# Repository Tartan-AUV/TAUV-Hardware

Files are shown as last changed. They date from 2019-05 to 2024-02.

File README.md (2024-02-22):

# TAUV-Hardware

Repository for TAUV Altium documents

# Boards:
## TAUV-PWR_STK
Next generation power management stack consisting of 2 boards. Manufacturing graciously sponsored by PCBway.com

## TAUV-Disconnect
Disconnect board for easy flange access

## TAUV-Interfacer
Utilizes a pair of STM32F7 processors to run hydrophone DOA estimates, and control/interface with LEDs, Servos, Jetson, and PowerBoard.

## TAUV-Acoustics Power Board
For powering the acoustics setup. Has low-noise 5V and 24V outputs.

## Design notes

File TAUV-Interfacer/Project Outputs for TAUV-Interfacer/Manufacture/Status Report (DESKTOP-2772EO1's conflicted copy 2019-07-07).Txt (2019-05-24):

Output: NC Drill Files
Type  : NC Drill
From  : PCB Document [TAUV-Interfacer.PcbDoc]
   Generated File[TAUV-Interfacer-RoundHoles.TXT]
   Generated File[TAUV-Interfacer-SlotHoles.TXT]
   Generated File[TAUV-Interfacer.DRL]
   Generated File[TAUV-Interfacer.LDP]
   Generated File[TAUV-Interfacer.DRR]

Files Generated   : 5
Documents Printed : 0

Finished Output Generation At 1:58:53 AM On 5/24/2019

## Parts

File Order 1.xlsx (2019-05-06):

Line # | Name | Description | Designator | Quantity | Manufacturer 1 | Manufacturer Part Number 1 | Manufacturer Lifecycle 1 | Supplier 1 | Supplier Part Number 1 | Supplier Unit Price 1 | Supplier Subtotal 1
 | #4-40 | Mounting Hole for ANSI #4-40 w/ Flat Washer, Loose Fit | MH1, MH2, MH3, MH4 | 8 |  |  |  |  |  |  |  | Power Board | Qtty: 2
 | 1K2 1% 0603(1608) | 1K2 0.1W 1% 0603 (1608 Metric) SMD | R37, R38 | 4 | Yageo (https://octopart-clicks.com/click/altium?sku=311-1.20KHRCT-ND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) | RC0603FR-071K2L (https://octopart-clicks.com/click/altium?sku=311-1.20KHRCT-ND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) | Volume Production | Digi-Key | 311-1.20KHRCT-ND (https://octopart-clicks.com/click/altium?sku=311-1.20KHRCT-ND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) | 0.024 | 0.24
 | 1K65 1% 0603(1608) | 1K65 0.1W 1% 0603 (1608 Metric) SMD | R7 | 2 | Yageo (https://octopart-clicks.com/click/altium?sku=311-1.65KHRCT-ND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) | RC0603FR-071K65L (https://octopart-clicks.com/click/altium?sku=311-1.65KHRCT-ND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) | Volume Production | Digi-Key | 311-1.65KHRCT-ND (https://octopart-clicks.com/click/altium?sku=311-1.65KHRCT-ND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) | 0.1 | 0.2
 | 1K 1% 0603(1608) | 1K 0.1W 1% 0603 (1608 Metric) SMD | R17 | 2 | Yageo (https://octopart-clicks.com/click/altium?sku=311-1.00KHRCT-ND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) | RC0603FR-071KL (https://octopart-clicks.com/click/altium?sku=311-1.00KHRCT-ND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) | Volume Production | Digi-Key | 311-1.00KHRCT-ND (https://octopart-clicks.com/click/altium?sku=311-1.00KHRCT-ND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) | 0.1 | 0.2
 | 2-pin megafit RA |  | J1, J2, J3, J4, J5, J6, J7, J8 | 16 | Molex (https://octopart-clicks.com/click/altium?sku=WM10391-ND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) | 172064-0002 (https://octopart-clicks.com/click/altium?sku=WM10391-ND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) | Manual Solution | Digi-Key | WM10391-ND (https://octopart-clicks.com/click/altium?sku=WM10391-ND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) | 2.53 | 40.53
 | 4K7 1% 0603(1608) | 4K7 0.1W 1% 0603 (1608 Metric) SMD | R19, R20 | 4 | Yageo (https://octopart-clicks.com/click/altium?sku=311-4.70KHRCT-ND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) | RC0603FR-074K7L (https://octopart-clicks.com/click/altium?sku=311-4.70KHRCT-ND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) | Volume Production | Digi-Key | 311-4.70KHRCT-ND (https://octopart-clicks.com/click/altium?sku=311-4.70KHRCT-ND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) | 0.024 | 0.24
 | 4-Pin Molex Nano-Fit | NanoFit RA Hdr TH SR 4Ckt | P3 | 2 | Molex (https://octopart-clicks.com/click/altium?sku=WM16895-ND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) | 105313-1104 (https://octopart-clicks.com/click/altium?sku=WM16895-ND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) | Manual Solution | Digi-Key | WM16895-ND (https://octopart-clicks.com/click/altium?sku=WM16895-ND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) | 1.2 | 2.4
 | 6.8uH |  | L2 | 2 | Bourns (https://octopart-clicks.com/click/altium?sku=SRP5030TA-6R8MCT-ND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) | SRP5030TA-6R8M (https://octopart-clicks.com/click/altium?sku=SRP5030TA-6R8MCT-ND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) | Volume Production | Digi-Key | SRP5030TA-6R8MCT-ND (https://octopart-clicks.com/click/altium?sku=SRP5030TA-6R8MCT-ND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) | 1.68 | 3.36
 | 8-Pin 4x2 Molex Nano-Fit | NanoFit RA Hdr TH DR 8Ckt | P2 | 2 | Molex (https://octopart-clicks.com/click/altium?sku=WM15168-ND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) | 1053141308 (https://octopart-clicks.com/click/altium?sku=WM15168-ND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) | Unknown | Digi-Key | WM15168-ND (https://octopart-clicks.com/click/altium?sku=WM15168-ND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) | 3.04 | 6.08
 | 10K 1% 0603(1608) | 10K 0.1W 1% 0603 (1608 Metric) SMD | R13 | 2 | Yageo (https://octopart-clicks.com/click/altium?sku=311-10.0KHRCT-ND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) | RC0603FR-0710KL (https://octopart-clicks.com/click/altium?sku=311-10.0KHRCT-ND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) | Volume Production | Digi-Key | 311-10.0KHRCT-ND (https://octopart-clicks.com/click/altium?sku=311-10.0KHRCT-ND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) | 0.1 | 0.2
 | 16K5 1% 0603(1608) | 16K5 0.1W 1% 0603 (1608 Metric) SMD | R26 | 2 | Yageo (https://octopart-clicks.com/click/altium?sku=311-16.5KHRCT-ND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) | RC0603FR-0716K5L (https://octopart-clicks.com/click/altium?sku=311-16.5KHRCT-ND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) | Volume Production | Digi-Key | 311-16.5KHRCT-ND (https://octopart-clicks.com/click/altium?sku=311-16.5KHRCT-ND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) | 0.1 | 0.2
 | 22AR100KLFTR | TT Electronics BI 22AR100KLFTR SMT trim pot, 100k 20% | R16 | 2 | TT BI (https://octopart-clicks.com/click/altium?sku=987-1003-1-ND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) | 22AR100KLFTR (https://octopart-clicks.com/click/altium?sku=987-1003-1-ND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) | Volume Production | Digi-Key | 987-1003-1-ND (https://octopart-clicks.com/click/altium?sku=987-1003-1-ND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) | 1.38 | 2.76
 | 22K1 1% 0603(1608) | 22K1 0.1W 1% 0603 (1608 Metric) SMD | R5, R6 | 4 | Yageo (https://octopart-clicks.com/click/altium?sku=311-22.1KHRCT-ND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) | RC0603FR-0722K1L (https://octopart-clicks.com/click/altium?sku=311-22.1KHRCT-ND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) | Volume Production | Digi-Key | 311-22.1KHRCT-ND (https://octopart-clicks.com/click/altium?sku=311-22.1KHRCT-ND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) | 0.024 | 0.24
 | 51K 1% 0603(1608) | 51K 0.1W 1% 0603 (1608 Metric) SMD | R4 | 2 | Vishay (https://octopart-clicks.com/click/altium?sku=541-51.0KHCT-ND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) | CRCW060351K0FKEA (https://octopart-clicks.com/click/altium?sku=541-51.0KHCT-ND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) | Volume Production | Digi-Key | 541-51.0KHCT-ND (https://octopart-clicks.com/click/altium?sku=541-51.0KHCT-ND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) | 0.1 | 0.2
 | 69K8 1% 0603(1608) | 69K8 0.1W 1% 0603 (1608 Metric) SMD | R10 | 2 | Yageo (https://octopart-clicks.com/click/altium?sku=311-69.8KHRCT-ND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) | RC0603FR-0769K8L (https://octopart-clicks.com/click/altium?sku=311-69.8KHRCT-ND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) | Volume Production | Digi-Key | 311-69.8KHRCT-ND (https://octopart-clicks.com/click/altium?sku=311-69.8KHRCT-ND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) | 0.1 | 0.2
 | 86K6 1% 0603(1608) | 86K6 0.1W 1% 0603 (1608 Metric) SMD | R11 | 2 | Yageo (https://octopart-clicks.com/click/altium?sku=311-86.6KHRCT-ND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) | RC0603FR-0786K6L (https://octopart-clicks.com/click/altium?sku=311-86.6KHRCT-ND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) | Volume Production | Digi-Key | 311-86.6KHRCT-ND (https://octopart-clicks.com/click/altium?sku=311-86.6KHRCT-ND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) | 0.1 | 0.2
 | 100R 1% 0603(1608) | 100R 0.1W 1% 0603 (1608 Metric) SMD | R21, R22, R24, R25, R31, R34 | 12 | Bourns (https://octopart-clicks.com/click/altium?sku=CR0603-FX-1000ELFCT-ND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) | CR0603-FX-1000ELF (https://octopart-clicks.com/click/altium?sku=CR0603-FX-1000ELFCT-ND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) | Volume Production | Digi-Key | CR0603-FX-1000ELFCT-ND (https://octopart-clicks.com/click/altium?sku=CR0603-FX-1000ELFCT-ND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) | 0.02 | 0.24
 | 100R 5% 0603(1608) | 100R 0.1W 5% 0603 (1608 Metric) SMD | R27, R28, R29, R30, R32, R33, R35, R36, R41 | 18 | Bourns (https://octopart-clicks.com/click/altium?sku=CR0603-JW-101ELFCT-ND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) | CR0603-JW-101ELF (https://octopart-clicks.com/click/altium?sku=CR0603-JW-101ELFCT-ND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) | Volume Production | Digi-Key | CR0603-JW-101ELFCT-ND (https://octopart-clicks.com/click/altium?sku=CR0603-JW-101ELFCT-ND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) | 0.015 | 0.27
 | 105K 1% 0603(1608) | 105K 0.1W 1% 0603 (1608 Metric) SMD | R14, R15 | 4 | Yageo (https://octopart-clicks.com/click/altium?sku=311-105KHRCT-ND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) | RC0603FR-07105KL (https://octopart-clicks.com/click/altium?sku=311-105KHRCT-ND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) | Volume Production | Digi-Key | 311-105KHRCT-ND (https://octopart-clicks.com/click/altium?sku=311-105KHRCT-ND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) | 0.024 | 0.24
 | 162K 1% 0603(1608) | 162K 0.1W 1% 0603 (1608 Metric) SMD | R12 | 2 | Yageo (https://octopart-clicks.com/click/altium?sku=311-162KHRCT-ND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) | RC0603FR-07162KL (https://octopart-clicks.com/click/altium?sku=311-162KHRCT-ND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) | Volume Production | Digi-Key | 311-162KHRCT-ND (https://octopart-clicks.com/click/altium?sku=311-162KHRCT-ND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) | 0.1 | 0.2
 | 200K 1% 0603(1608) | 200K 0.1W 1% 0603 (1608 Metric) SMD | R3 | 2 | Yageo (https://octopart-clicks.com/click/altium?sku=311-200KHRCT-ND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) | RC0603FR-07200KL (https://octopart-clicks.com/click/altium?sku=311-200KHRCT-ND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) | Volume Production | Digi-Key | 311-200KHRCT-ND (https://octopart-clicks.com/click/altium?sku=311-200KHRCT-ND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) | 0.1 | 0.2
 | 220R 5% 0603(1608) | 220R 0.1W 5% 0603 (1608 Metric) SMD | R40 | 2 | Yageo (https://octopart-clicks.com/click/altium?sku=311-220GRCT-ND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) | RC0603JR-07220RL (https://octopart-clicks.com/click/altium?sku=311-220GRCT-ND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) | Volume Production | Digi-Key | 311-220GRCT-ND (https://octopart-clicks.com/click/altium?sku=311-220GRCT-ND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) | 0.1 | 0.2
 | 294K 1% 0603(1608) | 294K 0.1W 1% 0603 (1608 Metric) SMD | R23 | 2 | Yageo (https://octopart-clicks.com/click/altium?sku=311-294KHRCT-ND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) | RC0603FR-07294KL (https://octopart-clicks.com/click/altium?sku=311-294KHRCT-ND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) | Volume Production | Digi-Key | 311-294KHRCT-ND (https://octopart-clicks.com/click/altium?sku=311-294KHRCT-ND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) | 0.1 | 0.2
 | 330R 1% 0603(1608) | 330R 0.1W 1% 0603 (1608 Metric) SMD | R18 | 2 | Yageo (https://octopart-clicks.com/click/altium?sku=311-330HRCT-ND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) | RC0603FR-07330RL (https://octopart-clicks.com/click/altium?sku=311-330HRCT-ND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) | Volume Production | Digi-Key | 311-330HRCT-ND (https://octopart-clicks.com/click/altium?sku=311-330HRCT-ND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) | 0.1 | 0.2
 | 470R 1% 0603(1608) | 470R 0.1W 1% 0603 (1608 Metric) SMD | R39 | 2 | Yageo (https://octopart-clicks.com/click/altium?sku=311-470HRCT-ND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) | RC0603FR-07470RL (https://octopart-clicks.com/click/altium?sku=311-470HRCT-ND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) | Volume Production | Digi-Key | 311-470HRCT-ND (https://octopart-clicks.com/click/altium?sku=311-470HRCT-ND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) | 0.1 | 0.2
 | 560K 1% 0603(1608) | 560K 0.1W 1% 0603 (1608 Metric) SMD | R8 | 2 | Yageo (https://octopart-clicks.com/click/altium?sku=311-560KHRCT-ND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) | RC0603FR-07560KL (https://octopart-clicks.com/click/altium?sku=311-560KHRCT-ND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) | Volume Production | Digi-Key | 311-560KHRCT-ND (https://octopart-clicks.com/click/altium?sku=311-560KHRCT-ND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) | 0.1 | 0.2
 | 976R 1% 0603(1608) | 976R 0.1W 1% 0603 (1608 Metric) SMD | R9 | 2 | Yageo (https://octopart-clicks.com/click/altium?sku=311-976HRCT-ND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) | RC0603FR-07976RL (https://octopart-clicks.com/click/altium?sku=311-976HRCT-ND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) | Volume Production | Digi-Key | 311-976HRCT-ND (https://octopart-clicks.com/click/altium?sku=311-976HRCT-ND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) | 0.1 | 0.2
 | 7443330220 | SMD High Current Cube Inductor WE-HCC, L=2.20 µH | L3 | 2 | Wurth Electronics (https://octopart-clicks.com/click/altium?sku=732-2153-1-ND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) | 7443330220 (https://octopart-clicks.com/click/altium?sku=732-2153-1-ND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) | Volume Production | Digi-Key | 732-2153-1-ND (https://octopart-clicks.com/click/altium?sku=732-2153-1-ND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) | 2.25 | 4.5
 | BQ34Z100PWR-G1 | No Description Available | U7 | 2 | Texas Instruments (https://octopart-clicks.com/click/altium?sku=296-39949-1-ND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) | BQ34Z100PWR-G1 (https://octopart-clicks.com/click/altium?sku=296-39949-1-ND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) | Manual Solution | Digi-Key | 296-39949-1-ND (https://octopart-clicks.com/click/altium?sku=296-39949-1-ND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) | 4.2 | 8.4
 | CAP 1nF 25V 0603(1608) | CAP 1nF 25V ±20% 0603 (1608 Metric) Thickness 1mm SMD | C21 | 2 | Vishay Vitramon (https://octopart-clicks.com/click/altium?sku=720-1680-1-ND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) | VJ0603Y102MXXCW1BC (https://octopart-clicks.com/click/altium?sku=720-1680-1-ND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) | Volume Production | Digi-Key | 720-1680-1-ND (https://octopart-clicks.com/click/altium?sku=720-1680-1-ND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) | 0.17 | 0.34
 | CAP 1uF 25V 0603(1608) | CAP 1uF 25V ±10% 0603 (1608 Metric) Thickness 1mm SMD | C13, C14, C22, C25, C26 | 10 | Yageo (https://octopart-clicks.com/click/altium?sku=311-1445-1-ND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) | CC0603KRX5R8BB105 (https://octopart-clicks.com/click/altium?sku=311-1445-1-ND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) | Volume Production | Digi-Key | 311-1445-1-ND (https://octopart-clicks.com/click/altium?sku=311-1445-1-ND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) | 0.145 | 1.45
 | CAP 4.7uF 35V 1206(3216) | CAP 4.7uF 35V ±10% 1206 (3216 Metric) Thickness 1.9mm SMD | C3, C4, C9, C10, C18 | 10 | Samsung (https://octopart-clicks.com/click/altium?sku=1276-3178-1-ND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) | CL31B475KAHNNWE (https://octopart-clicks.com/click/altium?sku=1276-3178-1-ND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) | Manual Solution | Digi-Key | 1276-3178-1-ND (https://octopart-clicks.com/click/altium?sku=1276-3178-1-ND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) | 0.22 | 2.2
 | CAP 10nF 25V 0603(1608) | CAP 10nF 25V ±2% 0603 (1608 Metric) Thickness 1mm SMD | C23 | 2 | Yageo (https://octopart-clicks.com/click/altium?sku=311-1360-1-ND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) | CC0603KRX7R8BB103 (https://octopart-clicks.com/click/altium?sku=311-1360-1-ND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) | Manual Solution | Digi-Key | 311-1360-1-ND (https://octopart-clicks.com/click/altium?sku=311-1360-1-ND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) | 0.1 | 0.2
 | CAP 10uF 50V 1206(3216) | CAP 10uF 50V ±10% 1206 (3216 Metric) Thickness 1.9mm SMD | C5 | 2 | TDK (https://octopart-clicks.com/click/altium?sku=445-5998-1-ND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) | C3216X5R1H106K160AB (https://octopart-clicks.com/click/altium?sku=445-5998-1-ND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) | Manual Solution | Digi-Key | 445-5998-1-ND (https://octopart-clicks.com/click/altium?sku=445-5998-1-ND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) | 1.06 | 2.12
 | CAP 12pF 50V 0603(1608) | CAP 12pF 50V ±0.25pF 0603 (1608 Metric) Thickness 1mm SMD | C7 | 2 | Yageo (https://octopart-clicks.com/click/altium?sku=311-1059-1-ND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) | CC0603JRNPO9BN120 (https://octopart-clicks.com/click/altium?sku=311-1059-1-ND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) | Manual Solution | Digi-Key | 311-1059-1-ND (https://octopart-clicks.com/click/altium?sku=311-1059-1-ND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) | 0.1 | 0.2
 | CAP 22uF 16V 1206(3216) | CAP 22uF 16V ±20% 1206 (3216 Metric) Thickness 1.9mm SMD | C? | 2 | Samsung (https://octopart-clicks.com/click/altium?sku=1276-2728-1-ND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) | CL31A226MOCLNNC (https://octopart-clicks.com/click/altium?sku=1276-2728-1-ND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) | Manual Solution | Digi-Key | 1276-2728-1-ND (https://octopart-clicks.com/click/altium?sku=1276-2728-1-ND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) | 0.45 | 0.9
 | CAP 22uF 25V 1210(3225) | CAP 22uF 25V -20% to +80% 1210 (3225 Metric) Thickness 2.2mm SMD | C19, C20, C24 | 6 | Samsung (https://octopart-clicks.com/click/altium?sku=1276-3391-1-ND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) | CL32B226KAJNFNE (https://octopart-clicks.com/click/altium?sku=1276-3391-1-ND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) | Manual Solution | Digi-Key | 1276-3391-1-ND (https://octopart-clicks.com/click/altium?sku=1276-3391-1-ND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) | 0.98 | 5.88
 | CAP 47uF 16V 1206(3216) | CAP 47uF 16V ±20% 1206 (3216 Metric) Thickness 1.9mm SMD | C12 | 2 | Murata (https://octopart-clicks.com/click/altium?sku=490-5528-1-ND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) | GRM31CR61A476ME15L (https://octopart-clicks.com/click/altium?sku=490-5528-1-ND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) | Manual Solution | Digi-Key | 490-5528-1-ND (https://octopart-clicks.com/click/altium?sku=490-5528-1-ND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) | 0.84 | 1.68
 | CAP 75pF 25V 0603(1608) | CAP 75pF 25V ±1% 0603 (1608 Metric) Thickness 1mm SMD | C8 | 2 | KEMET (https://octopart-clicks.com/click/altium?sku=399-7958-1-ND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) | C0603C750J5GACTU (https://octopart-clicks.com/click/altium?sku=399-7958-1-ND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) | Manual Solution | Digi-Key | 399-7958-1-ND (https://octopart-clicks.com/click/altium?sku=399-7958-1-ND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) | 0.38 | 0.76
 | CAP 100nF 100V 0603(1608) | CAP 100nF 100V ±10% 0603 (1608 Metric) Thickness 1mm SMD | C2, C6, C15, C17, C27, C28, C29, C30 | 16 | Murata (https://octopart-clicks.com/click/altium?sku=490-3285-1-ND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) | GRM188R72A104KA35D (https://octopart-clicks.com/click/altium?sku=490-3285-1-ND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) | Volume Production | Digi-Key | 490-3285-1-ND (https://octopart-clicks.com/click/altium?sku=490-3285-1-ND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) | 0.193 | 3.09
 | CAP 100uF 10V 1206(3216) | CAP 100uF 10V ±20% 1206 (3216 Metric) Thickness 1.9mm SMD | C16 | 2 | TDK (https://octopart-clicks.com/click/altium?sku=445-6007-1-ND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) | C3216X5R1A107M160AC (https://octopart-clicks.com/click/altium?sku=445-6007-1-ND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) | Manual Solution | Digi-Key | 445-6007-1-ND (https://octopart-clicks.com/click/altium?sku=445-6007-1-ND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) | 1.73 | 3.46
 | CAP 680nF 50V 0603(1608) | CAP 680nF 50V ±10% 0603 (1608 Metric) Thickness 1mm SMD | C1 | 2 | TDK (https://octopart-clicks.com/click/altium?sku=445-11284-1-ND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) | C1608JB1H684M080AB (https://octopart-clicks.com/click/altium?sku=445-11284-1-ND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) | Manual Solution | Digi-Key | 445-11284-1-ND (https://octopart-clicks.com/click/altium?sku=445-11284-1-ND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) | 0.34 | 0.68
 | Fuse Holder 3588 | Keystone Electronics 3588 | F1, F2, F3 | 6 | Keystone Electronics (https://octopart-clicks.com/click/altium?sku=36-3588-ND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) | 3588 (https://octopart-clicks.com/click/altium?sku=36-3588-ND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) | Volume Production | Digi-Key | 36-3588-ND (https://octopart-clicks.com/click/altium?sku=36-3588-ND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) | 1.03 | 6.18
 | LED GREEN | led | D12, D13, D14, D15, D16 | 10 | Vishay Lite-On (https://octopart-clicks.com/click/altium?sku=160-1426-1-ND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) | LTST-C171KGKT (https://octopart-clicks.com/click/altium?sku=160-1426-1-ND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) | Volume Production | Digi-Key | 160-1426-1-ND (https://octopart-clicks.com/click/altium?sku=160-1426-1-ND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) | 0.225 | 2.25
 | LED GREEN | led LTST-C171KRKT | D9, D10, D11 | 6 | Vishay Lite-On (https://octopart-clicks.com/click/altium?sku=160-1426-1-ND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) | LTST-C171KGKT (https://octopart-clicks.com/click/altium?sku=160-1426-1-ND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) | Volume Production | Digi-Key | 160-1426-1-ND (https://octopart-clicks.com/click/altium?sku=160-1426-1-ND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) | 0.31 | 1.86
 | LED RED | led LTST-C171KRKT | D4, D5 | 4 | Vishay Lite-On (https://octopart-clicks.com/click/altium?sku=160-1427-1-ND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) | LTST-C171KRKT (https://octopart-clicks.com/click/altium?sku=160-1427-1-ND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) | Volume Production | Digi-Key | 160-1427-1-ND (https://octopart-clicks.com/click/altium?sku=160-1427-1-ND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) | 0.31 | 1.24
 | LED YELLOW | led LTST-C171KSKT | D6, D7, D8 | 6 | Vishay Lite-On (https://octopart-clicks.com/click/altium?sku=160-1428-1-ND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) | LTST-C171KSKT (https://octopart-clicks.com/click/altium?sku=160-1428-1-ND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) | Volume Production | Digi-Key | 160-1428-1-ND (https://octopart-clicks.com/click/altium?sku=160-1428-1-ND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) | 0.33 | 1.98
 | LMR23630-Q1 |  | U1, U2 | 4 | Texas Instruments (https://octopart-clicks.com/click/altium?manufacturer=Texas%20Instruments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) | LMR23630AFQDDARQ1 (https://octopart-clicks.com/click/altium?manufacturer=Texas%20Instruments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) | Unknown | Digi-Key | 296-45260-1-ND (https://octopart-clicks.com/click/altium?manufacturer=Texas%20Instruments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) | 3.97 | 15.88
 | MIC5021YM | High-Speed High-Side MOSFET Driver, 12 to 36 V, -40 to 85 degC, 8-Pin SOIC, RoHS, Tube | U6 | 2 | Microchip Micrel (https://octopart-clicks.com/click/altium?sku=576-2354-ND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) | MIC5021YM (https://octopart-clicks.com/click/altium?sku=576-2354-ND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) | Volume Production | Digi-Key | 576-2354-ND (https://octopart-clicks.com/click/altium?sku=576-2354-ND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) | 2.5 | 5
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

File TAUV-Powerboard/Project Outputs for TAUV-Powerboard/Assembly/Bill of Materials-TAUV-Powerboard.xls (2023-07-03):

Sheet: TAUV-Powerboard (OLD)
Line # | Name | Description | Designator | Quantity | Extra | Qtty (to purchase) | Manufacturer 1 | Manufacturer Part Number 1 | Manufacturer Lifecycle 1 | Supplier 1 | Supplier Part Number 1 | Supplier Unit Price 1 | Per board: | Extras: | Supplier Subtotal 1 | Total: | 283.704
 | 1K2 1% 0603(1608) | 1K2 0.1W 1% 0603 (1608 Metric) SMD | R1, R36, R44 | 3 | 2 | 8 | Yageo | RC0603FR-071K2L | Volume Production | Digi-Key | 311-1.20KHRCT-ND | 0.023 | 0.069 | 0.046 | 0.184 | Per Board: | 94.573
 | 2-pin megafit |  | J1, J2, J3, J4, J5, J6, J7, J8, J9 | 9 | 1 | 19 | Molex | 76825-0002 | Volume Production | Digi-Key | WM11969-ND | 0.993 | 8.937 | 0.993 | 18.867 | Extras: | 94.558
 | 4K7 1% 0603(1608) | 4K7 0.1W 1% 0603 (1608 Metric) SMD | R3, R7, R20, R30 | 4 | 2 | 10 | Yageo | RC0603FR-074K7L | Volume Production | Digi-Key | 311-4.70KHRCT-ND | 0.023 | 0.092 | 0.046 | 0.23
 | 6.8uH |  | L4 | 1 | 1 | 3 | Bourns | SRP5030TA-6R8M | Volume Production | Digi-Key | SRP5030TA-6R8MCT-ND | 1.68 | 1.68 | 1.68 | 5.04
 | 7K5 1% 0603(1608) | 7K5 0.1W 1% 0603 (1608 Metric) SMD | R21 | 1 | 1 | 3 | Yageo | RC0603FR-077K5L | Volume Production | Digi-Key | 311-7.50KHRCT-ND | 0.1 | 0.1 | 0.1 | 0.3
 | 10K 5% 0603(1608) | 10K 0.1W 5% 0603 (1608 Metric) SMD | R12, R15, R18, R22 | 4 | 2 | 10 | Yageo | RC0603JR-0710KL | Volume Production | Digi-Key | 311-10KGRCT-ND | 0.017 | 0.068 | 0.034 | 0.17
 | 14-Pin 2-Row Nano-Fit Right Angle | NanoFit Right Hdr TH DR 14Ckt | P1, P3 | 2 | 1 | 5 | Molex | 105314-1214 | Unknown | Digi-Key | WM16912-ND | 2.6 | 5.2 | 2.6 | 13
 | 16K5 1% 0603(1608) | 16K5 0.1W 1% 0603 (1608 Metric) SMD | R26 | 1 | 1 | 3 | Yageo | RC0603FR-0716K5L | Volume Production | Digi-Key | 311-16.5KHRCT-ND | 0.1 | 0.1 | 0.1 | 0.3
 | 22K1 1% 0603(1608) | 22K1 0.1W 1% 0603 (1608 Metric) SMD | R5, R6, R10, R11 | 4 | 2 | 10 | Yageo | RC0603FR-0722K1L | Volume Production | Digi-Key | 311-22.1KHRCT-ND | 0.023 | 0.092 | 0.046 | 0.23
 | 51K 1% 0603(1608) | 51K 0.1W 1% 0603 (1608 Metric) SMD | R9 | 1 | 1 | 3 | Vishay | CRCW060351K0FKEA | Volume Production | Digi-Key | 541-51.0KHCT-ND | 0.1 | 0.1 | 0.1 | 0.3
 | 88K7 1% 0603(1608) | 88K7 0.1W 1% 0603 (1608 Metric) SMD | R2, R4 | 2 | 1 | 5 | Yageo | RC0603FR-0788K7L | Volume Production | Digi-Key | 311-88.7KHRCT-ND | 0.023 | 0.046 | 0.023 | 0.115
 | 100R 1% 0603(1608) | 100R 0.1W 1% 0603 (1608 Metric) SMD | R19, R23, R24, R28, R31, R32 | 6 | 2 | 14 | Bourns | CR0603-FX-1000ELF | Volume Production | Digi-Key | CR0603-FX-1000ELFCT-ND | 0.02 | 0.12 | 0.04 | 0.28
 | 100R 5% 0603(1608) | 100R 0.1W 5% 0603 (1608 Metric) SMD | R16, R17, R25, R29, R33, R34, R35, R37, R38, R39, R43 | 11 | 2 | 24 | Bourns | CR0603-JW-101ELF | Volume Production | Digi-Key | CR0603-JW-101ELFCT-ND | 0.015 | 0.165 | 0.03 | 0.36
 | 200K 1% 0603(1608) | 200K 0.1W 1% 0603 (1608 Metric) SMD | R8 | 1 | 1 | 3 | Yageo | RC0603FR-07200KL | Volume Production | Digi-Key | 311-200KHRCT-ND | 0.1 | 0.1 | 0.1 | 0.3
 | 220R 5% 0603(1608) | 220R 0.1W 5% 0603 (1608 Metric) SMD | R41, R42 | 2 | 1 | 5 | Yageo | RC0603JR-07220RL | Volume Production | Digi-Key | 311-220GRCT-ND | 0.019 | 0.038 | 0.019 | 0.095
 | 294K 1% 0603(1608) | 294K 0.1W 1% 0603 (1608 Metric) SMD | R27 | 1 | 1 | 3 | Yageo | RC0603FR-07294KL | Volume Production | Digi-Key | 311-294KHRCT-ND | 0.1 | 0.1 | 0.1 | 0.3
 | 470R 1% 0603(1608) | 470R 0.1W 1% 0603 (1608 Metric) SMD | R40 | 1 | 1 | 3 | Yageo | RC0603FR-07470RL | Volume Production | Digi-Key | 311-470HRCT-ND | 0.1 | 0.1 | 0.1 | 0.3
 | BQ34Z100PWR-G1 | No Description Available | U10 | 1 | 1 | 3 | Texas Instruments | BQ34Z100PWR-G1 | Manual Solution | Digi-Key | 296-39949-1-ND | 4.2 | 4.2 | 4.2 | 12.6
 | CAP 1uF 25V 0603(1608) | CAP 1uF 25V ±10% 0603 (1608 Metric) Thickness 1mm SMD | C1, C4, C15, C17, C37, C39 | 6 | 2 | 14 | Yageo | CC0603KRX5R8BB105 | Volume Production | Digi-Key | 311-1445-1-ND | 0.069 | 0.414 | 0.138 | 0.966
 | CAP 4.7uF 35V 1206(3216) | CAP 4.7uF 35V ±10% 1206 (3216 Metric) Thickness 1.9mm SMD | C7, C8, C10, C12, C13, C14, C22, C23, C24, C29 | 10 | 4 | 24 | Samsung | CL31B475KAHNNWE | Manual Solution | Digi-Key | 1276-3178-1-ND | 0.22 | 2.2 | 0.88 | 5.28
 | CAP 10nF 25V 0603(1608) | CAP 10nF 25V ±2% 0603 (1608 Metric) Thickness 1mm SMD | C19, C40 | 2 | 1 | 5 | Yageo | CC0603KRX7R8BB103 | Manual Solution | Digi-Key | 311-1360-1-ND | 0.1 | 0.2 | 0.1 | 0.5
 | CAP 10uF 50V 1206(3216) | CAP 10uF 50V ±10% 1206 (3216 Metric) Thickness 1.9mm SMD | C27 | 1 | 1 | 3 | TDK | C3216X5R1H106K160AB | Manual Solution | Digi-Key | 445-5998-1-ND | 1.06 | 1.06 | 1.06 | 3.18
 | CAP 12pF 50V 0603(1608) | CAP 12pF 50V ±0.25pF 0603 (1608 Metric) Thickness 1mm SMD | C16 | 1 | 1 | 3 | Yageo | CC0603JRNPO9BN120 | Manual Solution | Digi-Key | 311-1059-1-ND | 0.1 | 0.1 | 0.1 | 0.3
 | CAP 22uF 16V 1206(3216) | CAP 22uF 16V ±20% 1206 (3216 Metric) Thickness 1.9mm SMD | C25 | 1 | 1 | 3 | Samsung | CL31A226MOCLNNC | Manual Solution | Digi-Key | 1276-2728-1-ND | 0.45 | 0.45 | 0.45 | 1.35
 | CAP 22uF 25V 1210(3225) | CAP 22uF 25V -20% to +80% 1210 (3225 Metric) Thickness 2.2mm SMD | C30, C33 | 2 | 1 | 5 | Samsung | CL32B226KAJNFNE | Manual Solution | Digi-Key | 1276-3391-1-ND | 0.98 | 1.96 | 0.98 | 4.9
 | CAP 30pF 50V 0603(1608) | CAP 30pF 50V ±10% 0603 (1608 Metric) Thickness 1mm SMD | C2, C5 | 2 | 1 | 5 | KEMET | C0603C300J5GACTU | Volume Production | Digi-Key | 399-9057-1-ND | 0.24 | 0.48 | 0.24 | 1.2
 | CAP 47uF 16V 1206(3216) | CAP 47uF 16V ±20% 1206 (3216 Metric) Thickness 1.9mm SMD | C9, C11, C26 | 3 | 1 | 7 | Murata | GRM31CR61A476ME15L | Manual Solution | Digi-Key | 490-5528-1-ND | 0.84 | 2.52 | 0.84 | 5.88
 | CAP 75pF 25V 0603(1608) | CAP 75pF 25V ±1% 0603 (1608 Metric) Thickness 1mm SMD | C20 | 1 | 1 | 3 | KEMET | C0603C750J5GACTU | Manual Solution | Digi-Key | 399-7958-1-ND | 0.38 | 0.38 | 0.38 | 1.14
 | CAP 100nF 10V 0603(1608) | CAP 100nF 10V ±10% 0603 (1608 Metric) Thickness 1mm SMD | C31, C38 | 2 | 1 | 5 | KEMET | C0603C104K8RACTU | Volume Production | Digi-Key | 399-1095-6-ND | 0.14 | 0.28 | 0.14 | 0.7
 | CAP 100nF 100V 0603(1608) | CAP 100nF 100V ±10% 0603 (1608 Metric) Thickness 1mm SMD | C3, C6, C21, C28, C32, C34, C35, C36 | 8 | 2 | 18 | Murata | GRM188R72A104KA35D | Volume Production | Digi-Key | 490-3285-1-ND | 0.193 | 1.544 | 0.386 | 3.474
 | CAP 680nF 50V 0603(1608) | CAP 680nF 50V ±10% 0603 (1608 Metric) Thickness 1mm SMD | C18 | 1 | 1 | 3 | TDK | C1608JB1H684M080AB | Manual Solution | Digi-Key | 445-11284-1-ND | 0.34 | 0.34 | 0.34 | 1.02
 | Fuse Holder 3588 | Keystone Electronics 3588 | F1, F2, F3, F4 | 4 | 1 | 9 | Keystone Electronics | 3588 | Volume Production | Digi-Key | 36-3588-ND | 1.03 | 4.12 | 1.03 | 9.27
 | LED GREEN | led | D1, D7, D8, D9, D11, D18, D19, D20, D21, D22 | 10 | 2 | 22 | Vishay Lite-On | LTST-C171KGKT | Volume Production | Digi-Key | 160-1426-1-ND | 0.215 | 2.15 | 0.43 | 4.73
 | LED RED | led LTST-C171KRKT | D4, D5, D14, D17 | 4 | 2 | 10 | Vishay Lite-On | LTST-C171KRKT | Volume Production | Digi-Key | 160-1427-1-ND | 0.215 | 0.86 | 0.43 | 2.15
 | LED YELLOW | led LTST-C171KSKT | D10, D12, D13 | 3 | 2 | 8 | Vishay Lite-On | LTST-C171KSKT | Volume Production | Digi-Key | 160-1428-1-ND | 0.31 | 0.93 | 0.62 | 2.48
 | LMR23630-Q1 |  | U1, U2, U4, U5 | 4 | 1 | 9 | Texas Instruments | LMR23630AFQDDARQ1 | Unknown | Digi-Key | 296-45260-1-ND | 3.97 | 15.88 | 3.97 | 35.73
 | MIC5021YM | High-Speed High-Side MOSFET Driver, 12 to 36 V, -40 to 85 degC, 8-Pin SOIC, RoHS, Tube | U6, U11 | 2 | 1 | 5 | Microchip Micrel | MIC5021YM | Volume Production | Digi-Key | 576-2354-ND | 2.43 | 4.86 | 2.43 | 12.15
 | MMBZ5V6ALT1G | 24 W Peak Power Zener Transient Voltage Suppressor, Dual Common Anode Zeners for ESD Protection, 3-Pin SOT-23, Pb-Free, Tape and Reel | D6 | 1 | 1 | 3 | ON Semiconductor | MMBZ5V6ALT1G | Volume Production | Digi-Key | MMBZ5V6ALT1GOSCT-ND | 0.2 | 0.2 | 0.2 | 0.6
 | NCP18XH103F03RB | NTC Thermistor, 10 KOhm, +/- 1%, 0.1 W, -40 to 125 degC, 0603 (1608 Metric), RoHS, Tape and Reel | RT1 | 1 | 1 | 3 | Murata | NCP18XH103F03RB | Volume Production | Digi-Key | 490-4800-1-ND | 0.23 | 0.23 | 0.23 | 0.69
 | NVF6P02T3G | Power MOSFET, -10 A, -20 V, P-Channel, 4-Pin SOT-223, Pb-Free, Tape and Reel | Q1, Q2 | 2 | 1 | 5 | ON Semiconductor | NTF6P02T3G | Not Recommended for New Design | Digi-Key | NTF6P02T3GOSCT-ND | 0.85 | 1.7 | 0.85 | 4.25
 | NVTR01P02LT1G | Power MOSFET, -20 V, -1.3 A, P-Channel, 3-Pin SOT-23, Pb-Free, Tape and Reel | Q3, Q4 | 2 | 1 | 5 | ON Semiconductor | NVTR01P02LT1G | Volume Production | Digi-Key | NVTR01P02LT1GOSCT-ND | 0.42 | 0.84 | 0.42 | 2.1
 | Part Number: CSD18563Q5A | No Description Available | U3, U8, U9 | 3 | 1 | 7 | Texas Instruments | CSD18563Q5A | Manual Solution | Digi-Key | 296-36511-1-ND | 1.62 | 4.86 | 1.62 | 11.34
 | Part Number: INA300AIDSQT | No Description Available | U12 | 1 | 1 | 3 | Texas Instruments | INA300AIDSQT | Volume Production | Digi-Key | 296-37474-1-ND | 1.49 | 1.49 | 1.49 | 4.47
 | SBRT15U50SP5-13 |  | D2, D15, D16 | 3 | 1 | 7 | Diodes | SBRT15U50SP5-13 | Volume Production | Digi-Key | SBRT15U50SP5-13DICT-ND | 0.86 | 2.58 | 0.86 | 6.02
 | SMAJ30CA | Transient Voltage Suppression Diode, 30 V, -65 to 150 degC, 2-Pin SMD, RoHS, Tape and Reel | D3 | 1 | 1 | 3 | Littelfuse | SMAJ30CA | Volume Production | Digi-Key | SMAJ30CALFCT-ND | 0.45 | 0.45 | 0.45 | 1.35
 | SN74HC164PW | 8-Bit Parallel-Out Serial Shift Registers, PW0014A, TUBE | U13 | 1 | 1 | 3 | Texas Instruments | SN74HC164PW | Volume Production | Digi-Key | SN74HC164PW-ND | 0.39 | 0.39 | 0.39 | 1.17
 | SN74LVC1G97QDCKRQ1 | Automotive Catalog Configurable Multiple-Function Gate, DCK0006A, LARGE T&R | U7 | 1 | 1 | 3 | Texas Instruments | SN74LVC1G97QDCKRQ1 | Volume Production | Digi-Key | 296-17671-1-ND | 0.42 | 0.42 | 0.42 | 1.26
 | SRP6540-8R2M |  | L1, L2 | 2 | 1 | 5 | Bourns | SRP6540-8R2M | Volume Production | Digi-Key | SRP6540-8R2MCT-ND | 1.49 | 2.98 | 1.49 | 7.45
 | SRP6540-100M | Inductor Power Shielded/Molded Wirewound 10uH 20% 100KHz Powdered Iron 4A 78.5mOhm DCR T/R | L3 | 1 | 1 | 3 | Bourns | SRP6540-100M | Manual Solution | Digi-Key | SRP6540-100MCT-ND | 1.49 | 1.49 | 1.49 | 4.47
 | Test Point Loop | Keyston Electronics 5001 Test Point Loop | TP1, TP2, TP3, TP4, TP5, TP6, TP7, TP8, TP9, TP10 | 10 | 3 | 23 | Keystone Electronics | 5001 | Volume Production | Digi-Key | 36-5001-ND | 0.335 | 3.35 | 1.005 | 7.705
 | WSLP59312 2mR 8W |  | R13, R14 | 2 | 1 | 5 | Vishay | WSLP59312L000FEA | Manual Solution | Digi-Key | 541-10013-1-ND | 3.15 | 6.3 | 3.15 | 15.75
 |  | Extras:
 |  | Solder Paste |  | 0 | 1 | 1 |  |  |  |  | SMD291AX50T3-ND | 12.98 | 0 | 12.98 | 12.98
 |  | Megafits |  | 9 | 1 | 19 |  |  |  |  | WM10385-ND | 0.422 | 3.798 | 0.422 | 8.018
 |  | MicroFit Panel Connector |  | 0 | 3 | 3 |  |  |  |  | 23-0430201600-ND | 0.93 | 0 | 2.79 | 2.79
 |  | MicroFit Mating Panel Connector |  | 0 | 3 | 3 |  |  |  |  | WM2490-ND | 0.96 | 0 | 2.88 | 2.88
 |  | MiniFit Panel Connector |  | 0 | 2 | 2 |  |  |  |  | 23-0039012241-ND | 1.32 | 0 | 2.64 | 2.64
 |  | MiniFit Mating Panel Connector |  | 0 | 2 | 2 |  |  |  |  | WM3711-ND | 1.24 | 0 | 2.48 | 2.48
 |  | Nanofit Connectors |  | 2 | 1 | 5 |  |  |  |  | WM15024-ND | 0.73 | 1.46 | 0.73 | 3.65
 |  | Microfit contacts male |  |  | 50 | 50 |  |  |  |  | WM1841CT-ND | 0.15 | 0 | 7.5 | 7.5
 |  | Microfit contacts female |  |  | 50 | 50 |  |  |  |  | WM1837CT-ND | 0.15 | 0 | 7.5 | 7.5
 |  | Minifit contacts |  |  | 35 | 35 |  |  |  |  | WM2501CT-ND | 0.059 | 0 | 2.065 | 2.065
 |  | Nanofit contacts |  |  | 35 | 35 |  |  |  |  | WM16864CT-ND | 0.163 | 0 | 5.705 | 5.705
 |  | Megafit Contacts |  |  | 30 | 30 |  |  |  |  | WM11981CT-ND | 0.25 | 0 | 7.5 | 7.5

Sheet: TAUV_Thruster-Board
Line # | Name | Description | Designator | Revision ID | Revision State | Revision Status | Quantity | Manufacturer 1 | Manufacturer Part Number 1 | Manufacturer Lifecycle 1 | Supplier 1 | Supplier Part Number 1 | Supplier Unit Price 1 | Supplier Subtotal 1 | Component Links
 | 0.1uF | CAP CER 0.1UF 10V X7R 0603 | C1, C2 |  | Unknown server |  | 2 | KEMET | C0603C104K8RACTU | Volume Production | Digi-Key | 399-C0603C104K8RAC7867CT-ND | 0.11 | 0.22 | https://www.digikey.com/en/products/detail/C0603C104K8RAC7867/399-C0603C104K8RAC7867CT-ND/411370
 | X7R | Capacitor | Cin1, Cout1 |  | Not managed |  | 2 | KEMET | C0603C105K3PACTU | Volume Production | Digi-Key | 399-C0603C105K3PAC7867CT-ND | 0.18 | 0.36 | https://www.digikey.com/en/products/detail/C0603C105K3PAC7867/399-C0603C105K3PAC7867CT-ND/3471569
 | SBRT15U50SP5-13 | 50V 15A Rectifier Schottky Diode | D1 |  | Unknown server |  | 1 | Diodes | SBRT15U50SP5-13 | Volume Production | Digi-Key | SBRT15U50SP5-13DICT-ND | 0.87 | 0.87 | https://www.digikey.com/en/products/detail/SBRT15U50SP5-13/SBRT15U50SP5-13DICT-ND/4567794
 | 1SMA5931BT3G | 1.5 W Zener Voltage Regulator, 2-Pin SMA, Pb-Free, Tape and Reel | D2 |  | Unknown server |  | 1 | Littelfuse Inc. | SZ1SMA18AT3G | Manual Solution | Digi-Key | F11508CT-ND | 0.57 | 0.57 | https://www.digikey.com/en/products/detail/littelfuse-inc/SZ1SMA18AT3G/5845534
 | LED RED | led LTST-C171KRKT | D3, D4 |  | Not managed |  | 2 | Vishay Lite-On | LTST-C171KRKT | Volume Production | Digi-Key | 160-1427-1-ND | 0.28 | 0.56 | https://www.digikey.com/en/products/detail/LTST-C171KRKT/160-1427-1-ND/386800
 |  |  | J1, J2, J3, J4, J5, J6, J7, J8 |  | Not managed |  | 8 | Molex | 76825-0002 | Volume Production | Digi-Key | WM11969-ND | 1.38 | 11.04 | https://www.digikey.com/en/products/detail/0768250002/WM11969-ND/5639611
 |  |  | J9 |  | Not managed |  | 1 | Molex | 76825-0002 | Volume Production | Digi-Key | WM11969-ND | 1.38 | 1.38 | https://www.digikey.com/en/products/detail/0768250002/WM11969-ND/5639611
 | UMPS-10-05.5-L-V-S-W-TR | CONN MPOWER 2MM FMALE 10POS GOLD | JB1 |  | Unknown server |  | 1 | Samtec Inc. | UMPS-10-03.5-L-V-S-W-TR | Manual Solution | Digi-Key | 612-UMPS-10-03.5-L-V-S-W-TRCT-ND | 8.13 | 8.13 | https://www.digikey.com/en/products/detail/samtec-inc/UMPS-10-03-5-L-V-S-W-TR/14670346
 | UMPS-04-03.5-L-V-S-W-TR | CONN MPOWER 2MM FMALE 4POS GOLD | JB2 |  | Unknown server |  | 1 | Samtec Inc. | UMPS-04-03.5-L-V-S-W-TR | Manual Solution | Digi-Key | 612-UMPS-04-03.5-L-V-S-W-TRCT-ND | 4.72 | 4.72 | https://www.digikey.com/en/products/detail/samtec-inc/UMPS-04-03-5-L-V-S-W-TR/14670320
 | 74477420 | SMD Power Inductor WE-PD2, L = 100 µH | L1 |  | Unknown server |  | 1 | Wurth Electronics | 74477420 | Volume Production | Mouser | 710-74477420 | 1.88 | 1.88 | https://mouser.com/ProductDetail/Wurth-Elektronik/74477420?qs=rS3zZhy2AQMRbX1Obdv9xw%3D%3D
 | #4-40 | Mounting Hole for ANSI #4-40 w/ Flat Washer, Loose Fit | MH1, MH2, MH3 |  | Not managed |  | 3
 | BSC0702LSATMA1 | No Description Available | Q1, Q4, Q5 |  | Not managed |  | 3 | Infineon | BSC0702LSATMA1 | Unknown | Mouser | 726-BSC0702LSATMA1 | 1.65 | 4.95 | https://mouser.com/ProductDetail/Infineon-Technologies/BSC0702LSATMA1?qs=u4fy%2FsgLU9NYVEIY04ctJg%3D%3D
 | NVTR01P02LT1G | Power MOSFET, -20 V, -1.3 A, P-Channel, 3-Pin SOT-23, Pb-Free, Tape and Reel | Q2, Q3 |  | Unknown server |  | 2 | ON Semiconductor | NVTR01P02LT1G | Volume Production | Mouser | 863-NVTR01P02LT1G | 0.49 | 0.98 | https://mouser.com/ProductDetail/onsemi/NVTR01P02LT1G?qs=3PKVEWFFm2%2F%2FrLw71IHJjw%3D%3D
 | 0.1W 1% | 2k 0.1W 1% | R1 |  | Not managed |  | 1 | Panasonic | ERA3ARW202V | Volume Production | Digi-Key | P2.0KBECT-ND | 0.71 | 0.71 | https://www.digikey.com/en/products/detail/ERA-3ARW202V/P2.0KBECT-ND/3073308
 | 10K | 10K 0.1W 5% 0603 (1608 Metric) SMD | R2, Rin2 |  | Unknown server |  | 2 | Yageo | RC0603JR-0710KL | Volume Production | Digi-Key | 311-10KGRCT-ND | 0.014 | 0.14 | https://www.digikey.com/en/products/detail/RC0603JR-0710KL/311-10KGRCT-ND/729647
 | 100R | 100R 0.1W 5% | R3, R4 |  | Unknown server |  | 2 | Yageo | RC0603JR-07100RL | Volume Production | Digi-Key | 311-100GRCT-ND | 0.014 | 0.14 | https://www.digikey.com/en/products/detail/RC0603JR-07100RL/311-100GRCT-ND/729644
 | 0603 | Resistor | Rg |  | Not managed |  | 1 | Yageo | RC0603JR-07100RL | Volume Production | Digi-Key | 311-100GRCT-ND | 0.1 | 0.1 | https://www.digikey.com/en/products/detail/RC0603JR-07100RL/311-100GRCT-ND/729644
 | 0603 | Resistor | Rin1 |  | Not managed |  | 1 | Yageo | RC0603JR-0710KL | Volume Production | Digi-Key | 311-10KGRCT-ND | 0.1 | 0.1 | https://www.digikey.com/en/products/detail/RC0603JR-0710KL/311-10KGRCT-ND/729647
 | 0603 | Resistor | Rs |  | Not managed |  | 1 | Vishay Dale | CRCW060310R0JNEAHP | Volume Production | Digi-Key | 541-10SACT-ND | 0.15 | 0.15 | https://www.digikey.com/en/products/detail/CRCW060310R0JNEAHP/541-10SACT-ND/2222799
 | WSLP59312 2mR 8W |  | Rs1, Rs2 |  | Not managed |  | 2 | Vishay | WSLP59312L000FEA | Volume Production | Digi-Key | 541-10013-1-ND | 2.76 | 5.52 | https://www.digikey.com/en/products/detail/WSLP59312L000FEA/541-10013-1-ND/9758450
 | AUIR3241STR | IC GATE DRVR HIGH-SIDE 8SO | U1 |  | Unknown server |  | 1 | Infineon Technologies | AUIR3241STR | Manual Solution | Digi-Key | AUIR3241SCT-ND | 3.61 | 3.61 | https://www.digikey.com/en/products/detail/infineon-technologies/AUIR3241STR/7428056
 | SN74LVC1G97DBVR | IC CONFIG MULT-FUNC GATE SOT23-6 | U2 |  | Unknown server |  | 1 | Texas Instruments | SN74LVC1G97DBVR | Volume Production | Digi-Key | 296-15581-1-ND | 0.39 | 0.39 | https://www.digikey.com/en/products/detail/SN74LVC1G97DBVR/296-15581-1-ND/571166
 | Part Number: INA300AIDSQT | No Description Available | U3 |  | Not managed |  | 1 | Texas Instruments | INA300AIDSQT | Volume Production | Digi-Key | 296-37474-1-ND | 1.82 | 1.82 | https://www.digikey.com/en/products/detail/texas-instruments/INA300AIDSQT/4759519
 |  |  |  |  |  |  |  |  |  |  |  |  |  | Total Per Board:
 |  |  |  |  |  |  |  |  |  |  |  |  |  | 48.34
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

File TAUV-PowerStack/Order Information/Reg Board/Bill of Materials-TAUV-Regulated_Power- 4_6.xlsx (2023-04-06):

Comment | Description | Designator | Footprint | LibRef | Quantity | Available MFPN | Link | Substition Notes | DNP? | DNP For Assembly? | DNP Reason
100nF | CAP 100nF 100V ±10% 0603 (1608 Metric) Thickness 1mm SMD | C1, C8, C9 | CAPC0603(1608)100_L | CMP-1035-02595-1 | 3 | CL10B104KC8NNNC | https://www.digikey.com/en/products/detail/samsung-electro-mechanics/CL10B104KC8NNNC/5961291 | Any | No | No | N/A
4.7uF | CAP 4.7uF 35V ±10% 1206 (3216 Metric) Thickness 1.9mm SMD | C2, C3, C5, C10, C11, C12, C13, C16, C17 | CAPC1206(3216)190_L | CMP-1037-04922-1 | 9 | CL31B475KBHNFNE | https://www.digikey.com/en/products/detail/samsung-electro-mechanics/CL31B475KBHNFNE/3888837 | Any | No | No | N/A
75pF | CAP 75pF 25V ±1% 0603 (1608 Metric) Thickness 1mm SMD | C4 | CAPC0603(1608)100_L | CMP-1035-01189-1 | 1 | CC0603FRNPO9BN750 | https://www.digikey.com/en/products/detail/yageo/CC0603FRNPO9BN750/5883517 | Any | No | No | N/A
47uF | CAP 47uF 16V ±20% 1206 (3216 Metric) Thickness 1.9mm SMD | C6, C18, C19 | CAPC1206(3216)190_L | CMP-1037-05003-1 | 3 | EMK316BBJ476ML-T | https://www.digikey.com/en/products/detail/taiyo-yuden/EMK316BBJ476ML-T/7067010 | Any | No | No | N/A
1uF 25V | CAP 1uF 25V ±10% 0603 (1608 Metric) Thickness 1mm SMD | C7, C20, C21 | CAPC0603(1608)100_L | CMP-1035-02740-1 | 3 | CL10A105KA8NNNC | https://www.digikey.com/en/products/detail/samsung-electro-mechanics/CL10A105KA8NNNC/3886760 | Any | No | No | N/A
30pF | CAP 30pF 50V ±10% 0603 (1608 Metric) Thickness 1mm SMD | C14, C15 | CAPC0603(1608)100_L | CMP-1035-00915-1 | 2 | CML0603C0G300JT50V | https://www.digikey.com/en/products/detail/stackpole-electronics-inc/CML0603C0G300JT50V/10659967 | Any | No | No | N/A
08053C104KAT2A | CAP 0.1uF 25V ±10% 0805 (2012 Metric) SMD | Cbias1 | 805 | 08053C104KAT2A | 1 | 08053C104KAT2A | https://www.digikey.com/en/products/detail/kyocera-avx/08053C104KAT2A/1116281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 | Any | No | No | N/A
06033C104KAT2A | CAP 0.1uF 25V ±10% 0603 (1608 Metric) SMD | Cboot1, Cboot2 | 603 | 06033C104KAT2A | 2 | 06033C104KAT2A | https://www.digikey.com/en/products/detail/kyocera-avx/06033C104KAT2A/1116240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 | Any | No | No | N/A
50SVPF39M | CAP ALUM POLY 39UF 20% 50V SMD | Cbulk_1, Cbulk_2 | CAPSMT_62_E12 | 50SVPF39M | 2 | 50SVPF39M | https://www.digikey.com/en/products/detail/panasonic-electronic-components/50SVPF39M/4204925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 | Any | No | No | N/A
CL21C471JBANNNC | 470 pF ±5% 50V Ceramic Capacitor C0G, NP0 0805 (2012 Metric) | Ccomp1 | 805 | CL21C471JBANNNC | 1 | C0805C471J5GAC7210 | https://www.digikey.com/en/products/detail/kemet/C0805C471J5GAC7210/12701387 | Any (the commented part is no longer avaiable, use this CAP or any substitues) | No | No | N/A
CGA2B3X7R1H103K0 | CAP CER 10000PF 50V X7R 0402 | Ccomp2, Ccomp3 | 402 | CGA2B3X7R1H103K0 | 2 | CGA2B3X7R1H103K050BB | https://www.digikey.com/en/products/detail/tdk-corporation/CGA2B3X7R1H103K050BB/2672786 | Any | No | No | N/A
06035A470JAT2A | CAP CER 47PF 50V C0G/NP0 0603 | Ccs1 | 603 | 06035A470JAT2A | 1 | 06035A470JAT2A | https://www.digikey.com/en/products/detail/kyocera-avx/06035A470JAT2A/563281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 | Any | No | No | N/A
CGA3E2X7R1H104K080AA | CAP CER 0.1UF 50V X7R 0603 | Cf1 | 603 | CGA3E2X7R1H104K080AA | 1 | CGA3E2X7R1H104K080AA | https://www.digikey.com/en/products/detail/tdk-corporation/CGA3E2X7R1H104K080AA/2443144 | Any | No | No | N/A
35SVPF22M | CAP ALUM POLY 22UF 20% 35V SMD | Cin_1, Cin_2, Cin_3 | CAPSMT_62_F61 | 35SVPF22M | 3 | 35SVPF22M | https://www.digikey.com/en/products/detail/panasonic-electronic-components/35SVPF22M/4204892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 | Any | No | No | N/A
16SVPF180M | CAP ALUM POLY 180UF 20% 16V SMD | Cout_1, Cout_2, Cout_3 | CAPSMT_62_C10 | 16SVPF180M | 3 | 16SVPF180M | https://www.digikey.com/en/products/detail/panasonic-electronic-components/16SVPF180M/4204811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 | Max mounted height <6.5mm | No | No | N/A
C2012X5R1V226M12 | CAP CER 22UF 35V X5R 0805 | Coutx1, Coutx2, Coutx3 | 805 | C2012X5R1V226M12 | 3 | C2012X5R1V226M12 | https://www.digikey.com/en/products/detail/tdk-corporation/C2012X5R1V226M125AC/3951664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 | Any | No | No | N/A
CC0603JRNPO9BN18 | CAP CER 18PF 50V C0G/NPO 0603 | Cslope1, Css1 | 603 | CC0603JRNPO9BN18 | 2 | CC0603JRNPO9BN180 | https://www.digikey.com/en/products/detail/yageo/CC0603JRNPO9BN180/302795 | Any | No | No | N/A
EMK107B7105KA-T | CAP CER 1UF 16V X7R 0603 | Cvcc1 | 603 | EMK107B7105KA-T | 1 | EMK107B7105KA-T | https://www.digikey.com/en/products/detail/taiyo-yuden/EMK107B7105KA-T/930593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 | Any | No | No | N/A
LED RED | LED RED CLEAR SMD | D1 | C0805 | LED0 | 1 | LTST-C171KRKT | https://www.digikey.com/en/products/detail/liteon/LTST-C171KRKT/386801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 | Any | No | No | N/A
LED GREEN | LED GREEN CLEAR SMD | D2, D3, D5, D6, D7, D8 | LED_0805 | LED0 | 6 | LTST-C191KGKT | https://www.digikey.com/en/products/detail/liteon/LTST-C191KGKT/386835 | Any | No | No | N/A
SBRT15U50SP5-13 | DIODE SBR 50V 15A POWERDI5 | D9 | SBRT15U50SP5-13 | SBRT15U50SP5-13 | 1 | SBRT15U50SP5-13 | https://www.digikey.com/en/products/detail/diodes-incorporated/SBRT15U50SP5-13/4567773 | Any | No | No | N/A
SMAJ30CA | TVS DIODE 30VWM 48.4VC DO214AC | D10 | LFUS-DO-214AC-A-2_V | CMP-2000-07088-1 | 1 | SMAJ30CA | https://www.digikey.com/en/products/detail/littelfuse-inc/SMAJ30CA/762295 | Any | No | No | N/A
CDBK0540-HF | Diode 40 V 500mA Surface Mount SOD-123F | Dboot1, Df1 | SOD-123F | CDBK0540-HF | 2 | RBR1MM40ATR | https://www.digikey.com/en/products/detail/rohm-semiconductor/RBR1MM40ATR/5813370 | Any | No | No | N/A
CDBK0520L-HF | DIODE SCHOTTKY 20V 500MA SOD123F | Dboot2 | SOD-123F | CDBK0520L-HF | 1 | SM5817PL-TP | https://www.digikey.com/en/products/detail/micro-commercial-co/SM5817PL-TP/1793251 | Any | No | No | N/A
UMPT-10-01.5-L-V-S-W-TR | CONN MPOWER 2MM MALE 10POS GOLD | J1 | FP-UMPT-10-01_5-L-V-S-W-T-MFG | CMP-02770-000045-1 | 1 | UMPT-10-01.5-L-V-S-W-TR | https://www.digikey.com/en/products/detail/samtec-inc/UMPT-10-01-5-L-V-S-W-TR/14670365 | Any | No | No | N/A
TSW-115-05-G-S | CONN HEADER VERT 15POS 2.54MM | J2, J3 | SAMTEC_TSW-115-05-G-S | TSW-115-05-G-S | 2 | TSW-115-05-G-S | https://www.digikey.com/en/products/detail/samtec-inc/TSW-115-05-G-S/1100506 | Any | No | No | N/A
XAL1010-152MEB | 1.5 µH Shielded Molded Inductor 40.5 A 1.76mOhm Max Nonstandard | L1 | XAL1010 | XAL1010-152MEB | 1 | XAL1010-152MED | https://www.digikey.com/en/products/detail/coilcraft/XAL1010-152MED/15794456 | Any | No | No | N/A
6.8uH | FIXED IND 6.8UH 4A 76.2 MOHM SMD | L2 | BOURNS SRP5030T | SRP5030TA | 1 | SRP5030TA-6R8M | https://www.digikey.com/en/products/detail/bourns-inc/SRP5030TA-6R8M/5429675 | Any | No | No | N/A
SRP6540-8R2M | FIXED IND 8.2UH 4.5A 50.5MOHM SM | L3, L4 | BOURNS SRP5030T | SRP5030TA_8R2 | 2 | SRP6540-8R2M | https://www.digikey.com/en/products/detail/bourns-inc/SRP6540-8R2M/3986098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 | Any | No | No | N/A
CSD17577Q5A | N-Channel 30 V 60A (Ta) 3W (Ta), 53W (Tc) Surface Mount 8-VSONP (5x6) | M1 | TRANS_NexFET_Q5A | CSD17577Q5A | 1 | CSD17577Q5A | https://www.digikey.com/en/products/detail/texas-instruments/CSD17577Q5A/4965737 | Any | No | No | N/A
CSD17303Q5 | MOSFET N-CH 30V 32A/100A 8VSON | M2 | TRANS_NexFET_Q5 | CSD17303Q5 | 1 | CSD17303Q5 | https://www.digikey.com/en/products/detail/texas-instruments/CSD17303Q5/2263832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 | Any | No | No | N/A
CSD18537NQ5A | MOSFET N-CH 60V 50A 8VSON | M3 | TRANS_NexFET_Q5A | CSD18537NQ5A | 1 | CSD18537NQ5A | https://www.digikey.com/en/products/detail/texas-instruments/CSD18537NQ5A/4279646 | Any | No | No | N/A
CSD17573Q5B | MOSFET N-CH 30V 100A 8VSON | M4 | TRANS_NexFET_Q5 | CSD17573Q5B | 1 | CSD17573Q5B | https://www.digikey.com/en/products/detail/texas-instruments/CSD17573Q5B/4914143 | Any | No | No | N/A
#4-40 | Mounting Hole for ANSI #4-40 w/ Flat Washer, Loose Fit | MH1, MH2, MH3, MH4, MH5, MH6, MH7 | Mounting Hole #4-40 | Mounting Hole #4-40, Loose Fit | 7 |  |  | Any | Yes | Yes | Not a component
14-Pin 2-Row Nano-Fit Right Angle | CONN HEADER R/A 14POS 2.5MM | P1, P2, P4, P5 | MOLEX NANO-FIT 2X7 - Right Angle | 14-Pin 2-Row Nano-Fit Right Angle | 4 | 1053141114 | https://www.digikey.com/en/products/detail/molex/1053141114/7693193 | Any | No | Yes | Easy to do in house
XT90 |  | P3 | XT90 | XT90 | 1 |  |  | Any | Yes | Yes | May not be XT90 in final deployment
IRF9Z34STRLPBF | MOSFET P-CH 60V 18A D2PAK | Q1, Q2 | TO254P1521X483-4N | IRF9Z34STRLPBF | 2 | IRF9Z34STRLPBF | https://www.digikey.com/en/products/detail/vishay-siliconix/IRF9Z34STRLPBF/856689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 | Any | No | No | N/A
NVTR01P02LT1G | MOSFET P-CH 20V 1.3A SOT23-3 | Q3 | ONSC-SOT-23-3-318-08_V | CMP-1058-00752-1 | 1 | DMG2301L-7 | https://www.digikey.com/en/products/detail/diodes-incorporated/DMG2301L-7/5768820 | Any | No | No | N/A
51K 1% | 51K 0.1W 1% 0603 (1608 Metric) SMD | R1 | RESC0603(1608)_L | CMP-1012-00703-1 | 1 | RC0603FR-0751KL | https://www.digikey.com/en/products/detail/yageo/RC0603FR-0751KL/727282 | Any | No | No | N/A
22K1 1% | 22K1 0.1W 1% 0603 (1608 Metric) SMD | R2, R5, R6 | RESC0603(1608)_L | CMP-1012-00660-1 | 3 | RC0603FR-0722K1L | https://www.digikey.com/en/products/detail/yageo/RC0603FR-0722K1L/727058 | Any | No | No | N/A
88K7 1% | 88K7 0.1W 1% 0603 (1608 Metric) SMD | R3, R4 | RESC0603(1608)_L | CMP-1012-00730-1 | 2 | RC0603FR-0788K7L | https://www.digikey.com/en/products/detail/yageo/RC0603FR-0788K7L/727415 | Any | No | No | N/A
100R | RES 100 OHM 5% 1/10W 0603 | R7 | RESC1609X50X30NL10T20 | CMP-1012-00050-2 | 1 | RC0603JR-07100RL | https://www.digikey.com/en/products/detail/yageo/RC0603JR-07100RL/726697 | Any | No | No | N/A
1K2 | 1K2 0.1W 1% 0603 (1608 Metric) SMD | R8, R9 | RESC0603(1608)_L | CMP-1012-00518-1 | 2 | RC0603FR-131K2L | https://www.digikey.com/en/products/detail/yageo/RC0603FR-131K2L/14008161 | Any | No | No | N/A
CRCW0805470KFKEA | RES 470K OHM 1% 1/8W 0805 | R10, R17, R18, R19 | FP-CRCW0805-e3-IPC_C | CMP-2001-03930-2 | 4 | RC0805FR-07470KL | https://www.digikey.com/en/products/detail/yageo/RC0805FR-07470KL/727977 | Any | No | No | N/A
681R | 681R 0.1W 1% 0603 (1608 Metric) SMD | R11 | RESC0603(1608)_L | CMP-1012-00492-1 | 1 | RC0603FR-07681RL | https://www.digikey.com/en/products/detail/yageo/RC0603FR-07681RL/727357 | Any | No | No | N/A
220R | 220R 0.1W 5% 0603 (1608 Metric) SMD | R12, R13 | RESC0603(1608)_L | CMP-1012-00058-1 | 2 | RC0603JR-07220RL | https://www.digikey.com/en/products/detail/yageo/RC0603JR-07220RL/726741 | Any | No | No | N/A
100R | 100R 0.1W 5% 0603 (1608 Metric) SMD | R14 | RESC0603(1608)_L | CMP-1012-00050-1 | 1 | RC0603JR-07100RL | https://www.digikey.com/en/products/detail/yageo/RC0603JR-07100RL/726697 | Any | No | No | N/A
4K7 | 4K7 0.1W 1% 0603 (1608 Metric) SMD | R15, R16 | RESC0603(1608)_L | CMP-1012-00586-1 | 2 | RC0603FR-074K7L | https://www.digikey.com/en/products/detail/yageo/RC0603FR-074K7L/727212 | Any | No | No | N/A
CRCW0805160KFKEA | RES Thick Film, 160kO, 1%, 0.125W, 100ppm/°C, 0805 | R20, R21, R22, R23 | FP-CRCW0805-e3-IPC_C | CMP-1013-00757-2 | 4 | RC0805FR-07160KL | https://www.digikey.com/en/products/detail/yageo/RC0805FR-07160KL/727628 | Any | No | No | N/A
CRCW08050000Z0EA | RES 0 OHM JUMPER 1/8W 0805 | R24, R25, R26, R27, R28, R29 | RESC2013X50X30LL20T20 | CMP-2001-04896-1 | 6 | RC0805JR-070RL | https://www.digikey.com/en/products/detail/yageo/RC0805JR-070RL/728216 | Any | No | No | N/A
CRCW040210K5FKED | RES SMD 10.5K OHM 1% 1/16W 0402 | Rcomp1 | 402 | CRCW040210K5FKED | 1 | RC0402FR-0710K5L | https://www.digikey.com/en/products/detail/yageo/RC0402FR-0710K5L/5280811 | Any | No | No | N/A
CRCW0603100RFKEA | RES 4.7K OHM 1% 1/10W 0603 | Rcsg1, Rcsp1 | 603 | CRCW0603100RFKEA | 2 | RC0603FR-074K7L | https://www.digikey.com/en/products/detail/yageo/RC0603FR-074K7L/727212 | Any | No | No | N/A
RC0603FR-0710RL | RES 10 OHM 1% 1/10W 0603 | Rf1 | 603 | RC0603FR-0710RL | 1 | RC0603FR-0710RL | https://www.digikey.com/en/products/detail/yageo/RC0603FR-0710RL/726879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 | Any | No | No | N/A
RC0603FR-0720KL | RES 20K OHM 1% 1/10W 0603 | Rfbb1 | 603 | RC0603FR-0720KL | 1 | RC0603FR-0720KL | https://www.digikey.com/en/products/detail/yageo/RC0603FR-0720KL/727040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 | Any | No | No | N/A
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

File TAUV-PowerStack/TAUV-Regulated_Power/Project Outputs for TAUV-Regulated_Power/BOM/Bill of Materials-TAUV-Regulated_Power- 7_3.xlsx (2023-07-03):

Comment | Description | Designator | Footprint | LibRef | Quantity | Link | MPN | Price per | Total | DNP? | Allow Substitute?
100nF | CAP 100nF 100V ±10% 0603 (1608 Metric) Thickness 1mm SMD | C1, C9,C23, C61 | CAPC0603(1608)100_L | CMP-1035-02595-1 | 5 | https://www.digikey.com/en/products/detail/samsung-electro-mechanics/CL10B104KC8NNNC/5961291 | CL10B104KC8NNNC | 0.1 | 0.5 |  | Yes
4.7uF | CAP 4.7uF 35V ±10% 1206 (3216 Metric) Thickness 1.9mm SMD | C2, C3, C5, C12, C13, C17 | CAPC1206(3216)190_L | CMP-1037-04922-1 | 6 | https://www.digikey.com/en/products/detail/samsung-electro-mechanics/CL31B475KBHNFNE/3888837 | CL31B475KBHNFNE | 0.3 | 1.8 |  | Yes
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

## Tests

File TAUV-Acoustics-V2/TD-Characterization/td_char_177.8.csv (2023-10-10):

;Scopy version | f4beeb1
;Exported on | Saturday October 07/10/2023
;Device | M2K
;Nr of samples | 1000
;Sample rate | 0
;Tool | Network Analyzer
;Additional Information | Reference channel: 1
Sample | Frequency(Hz) | Magnitude(dB) | Phase(°)
0 | 100000 | 20.3728 | -3.44949
1 | 100231 | -0.229332 | -3.77189
2 | 100462 | -0.225074 | -3.89699
3 | 100694 | -0.225266 | -3.79074
4 | 100926 | -0.226386 | -3.83344
5 | 101159 | -0.243387 | -3.85726
6 | 101393 | -0.236412 | -3.89436
7 | 101627 | -0.228103 | -3.93655
8 | 101861 | -0.233463 | -3.87676
9 | 102096 | -0.227137 | -3.92533
10 | 102332 | -0.236516 | -3.84496
11 | 102568 | -0.244107 | -4.05355
12 | 102804 | -0.234427 | -3.93404
13 | 103042 | -0.231809 | -3.91778
14 | 103279 | -0.231818 | -3.9106
15 | 103518 | -0.232424 | -3.96605
16 | 103757 | -0.235125 | -4.01208
17 | 103996 | -0.237515 | -3.93027
18 | 104236 | -0.246914 | -3.94024
19 | 104477 | -0.233847 | -3.97452
20 | 104718 | -0.229982 | -3.95466
21 | 104959 | -0.238964 | -3.98921
22 | 105202 | -0.234417 | -4.04153
23 | 105444 | -0.247139 | -3.97962
24 | 105688 | -0.232852 | -3.97909
25 | 105931 | -0.244197 | -4.05344
26 | 106176 | -0.244847 | -4.14682
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

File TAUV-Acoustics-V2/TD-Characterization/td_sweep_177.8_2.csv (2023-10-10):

;Scopy version | f4beeb1
;Exported on | Saturday October 07/10/2023
;Device | M2K
;Nr of samples | 1000
;Sample rate | 0
;Tool | Network Analyzer
;Additional Information | Reference channel: 1
Sample | Frequency(Hz) | Magnitude(dB) | Phase(°)
0 | 100000 | 20.3667 | -4.31661
1 | 100231 | -0.230191 | -4.71754
2 | 100462 | -0.241176 | -4.72418
3 | 100694 | -0.241379 | -4.70557
4 | 100926 | -0.24216 | -4.73855
5 | 101159 | -0.234719 | -4.80075
6 | 101393 | -0.238982 | -4.74171
7 | 101627 | -0.240956 | -4.79018
8 | 101861 | -0.237909 | -4.80497
9 | 102096 | -0.238397 | -4.75331
10 | 102332 | -0.236481 | -4.76153
11 | 102568 | -0.25045 | -4.88892
12 | 102804 | -0.240722 | -4.82369
13 | 103042 | -0.233873 | -4.81754
14 | 103279 | -0.242899 | -4.86899
15 | 103518 | -0.252043 | -4.79837
16 | 103757 | -0.249681 | -4.86976
17 | 103996 | -0.247845 | -4.89248
18 | 104236 | -0.241808 | -4.88773
19 | 104477 | -0.23469 | -4.89499
20 | 104718 | -0.244557 | -4.9514
21 | 104959 | -0.237856 | -4.85946
22 | 105202 | -0.242333 | -4.91789
23 | 105444 | -0.24692 | -4.84847
24 | 105688 | -0.252274 | -4.90283
25 | 105931 | -0.235782 | -4.97314
26 | 106176 | -0.237828 | -5.01063
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

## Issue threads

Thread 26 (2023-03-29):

Power system Rev B

rjmorgan11, 2023-03-29:
Add jumpers for turning on regulators and thrusters independently and without the need for a specialized connector.
Make it possible to activate and deactivate power lines at will (maybe even make it possible to power cycle the Jetson while in the water)
Other quality of life changes to be added
Integrate arduino or other microcontroller into the board? (This should be a separate version labeled as V2)

Closed 2024-02-22.

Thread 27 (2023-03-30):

Create official release of V1 Stack Rev A

rjmorgan11, 2023-03-30:
Include BOM of all boards in separate files, Libraries, and all files related to the function of the stack within the sub (reg board, thruster board, kill switch board)

Closed 2023-07-07.

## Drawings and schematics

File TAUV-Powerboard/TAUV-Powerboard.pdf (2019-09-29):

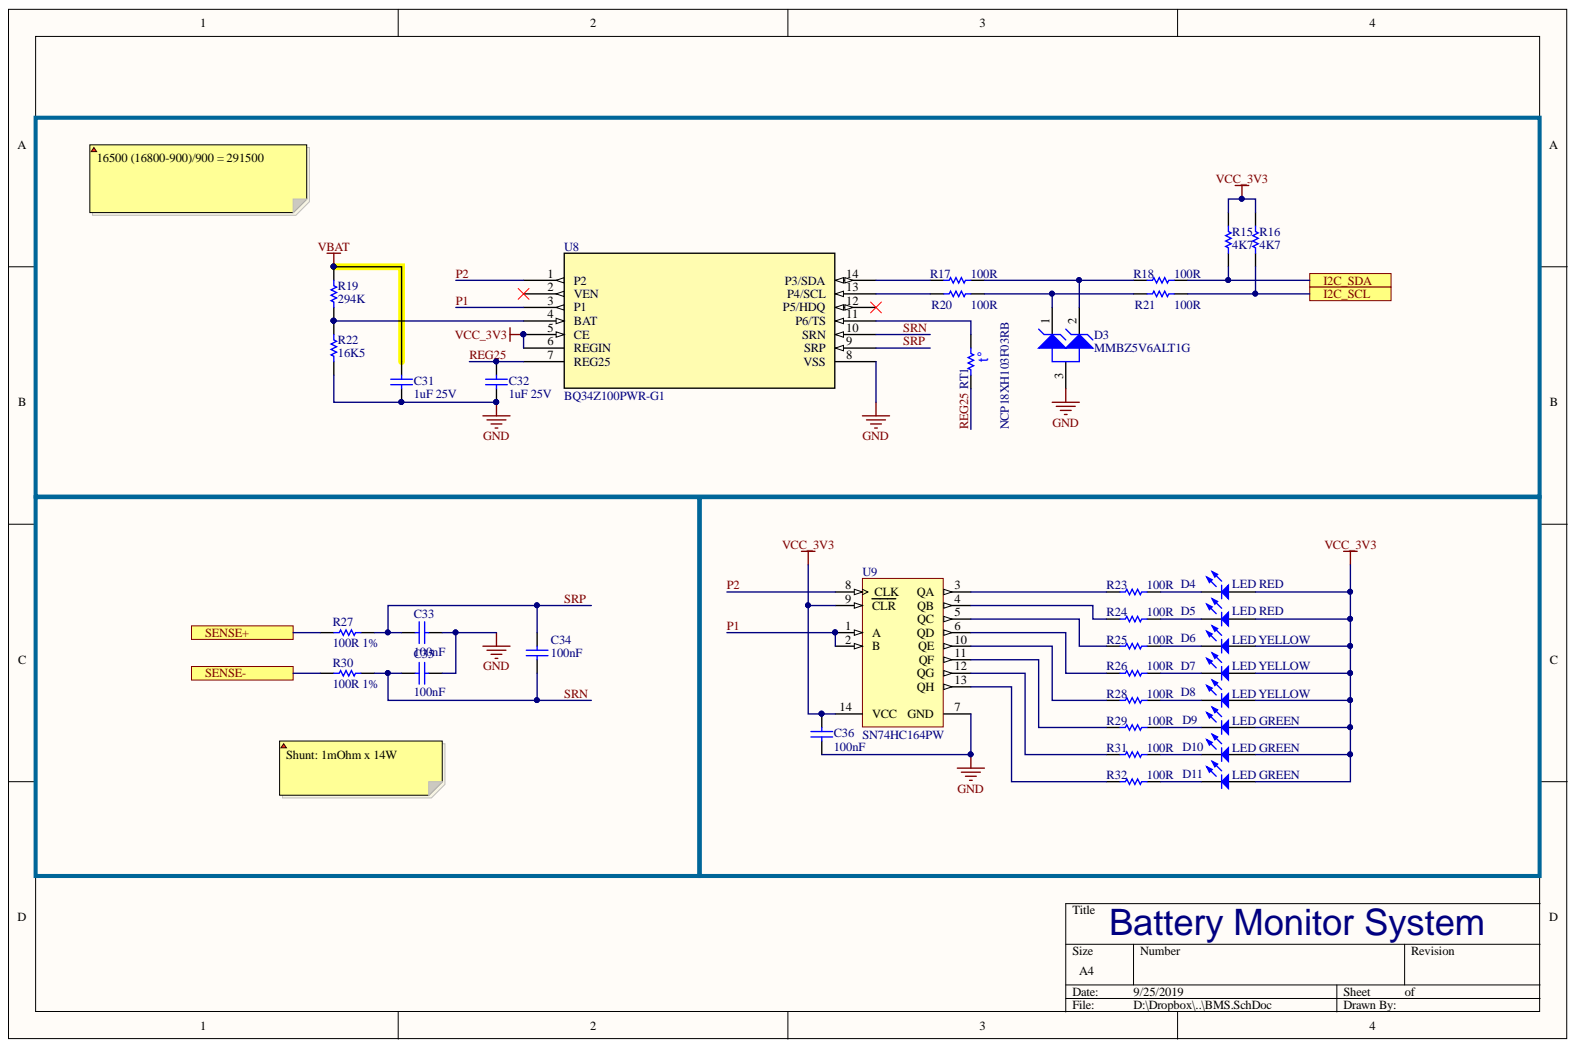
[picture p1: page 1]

Size A4 | Number | Revision

Date: 9/25/2019 | Sheet of
File: D:\Dropbox\..\BMS.SchDoc | Drawn By:

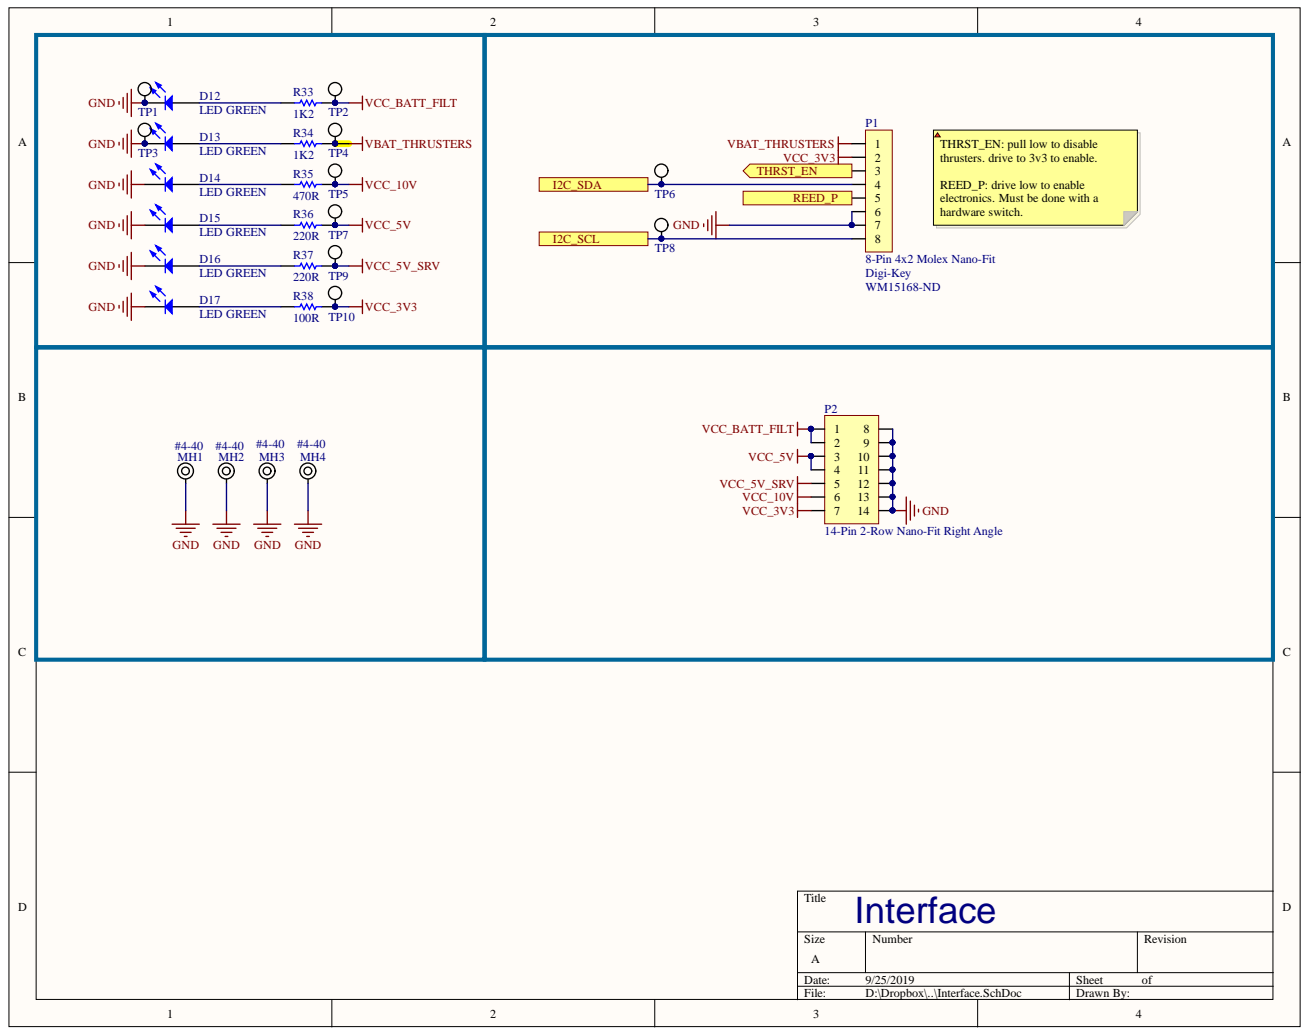
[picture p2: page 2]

THRST_EN: pull low to disable
thrusters. drive to 3v3 to enable.

REED_P: drive low to enable
electronics. Must be done with a
hardware switch.

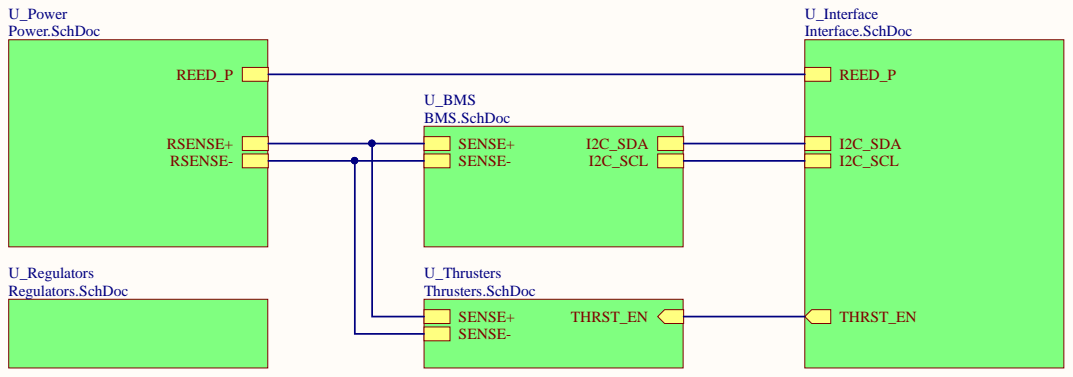
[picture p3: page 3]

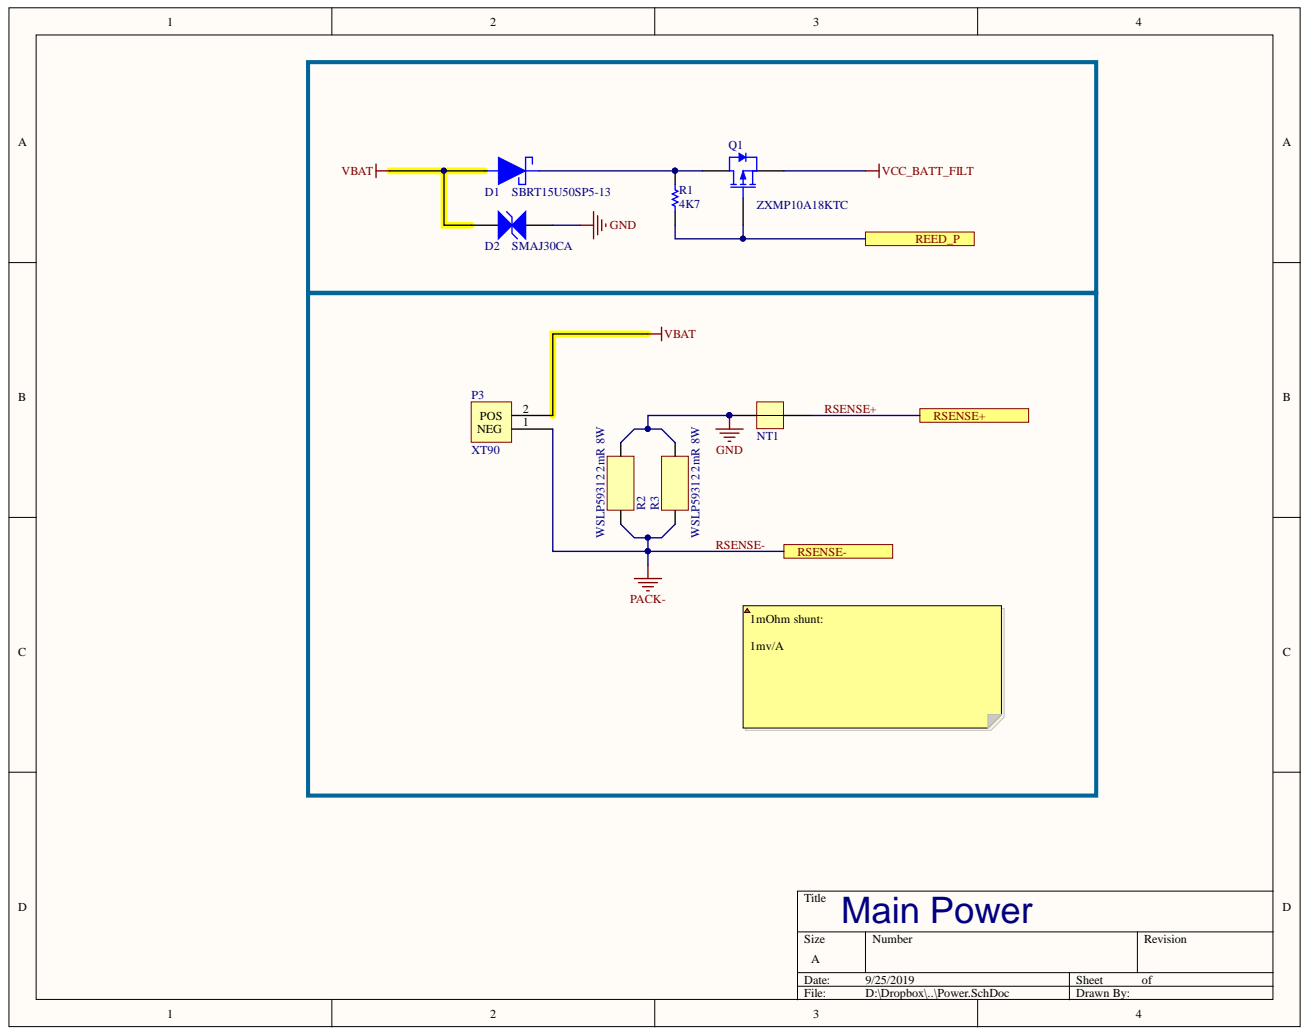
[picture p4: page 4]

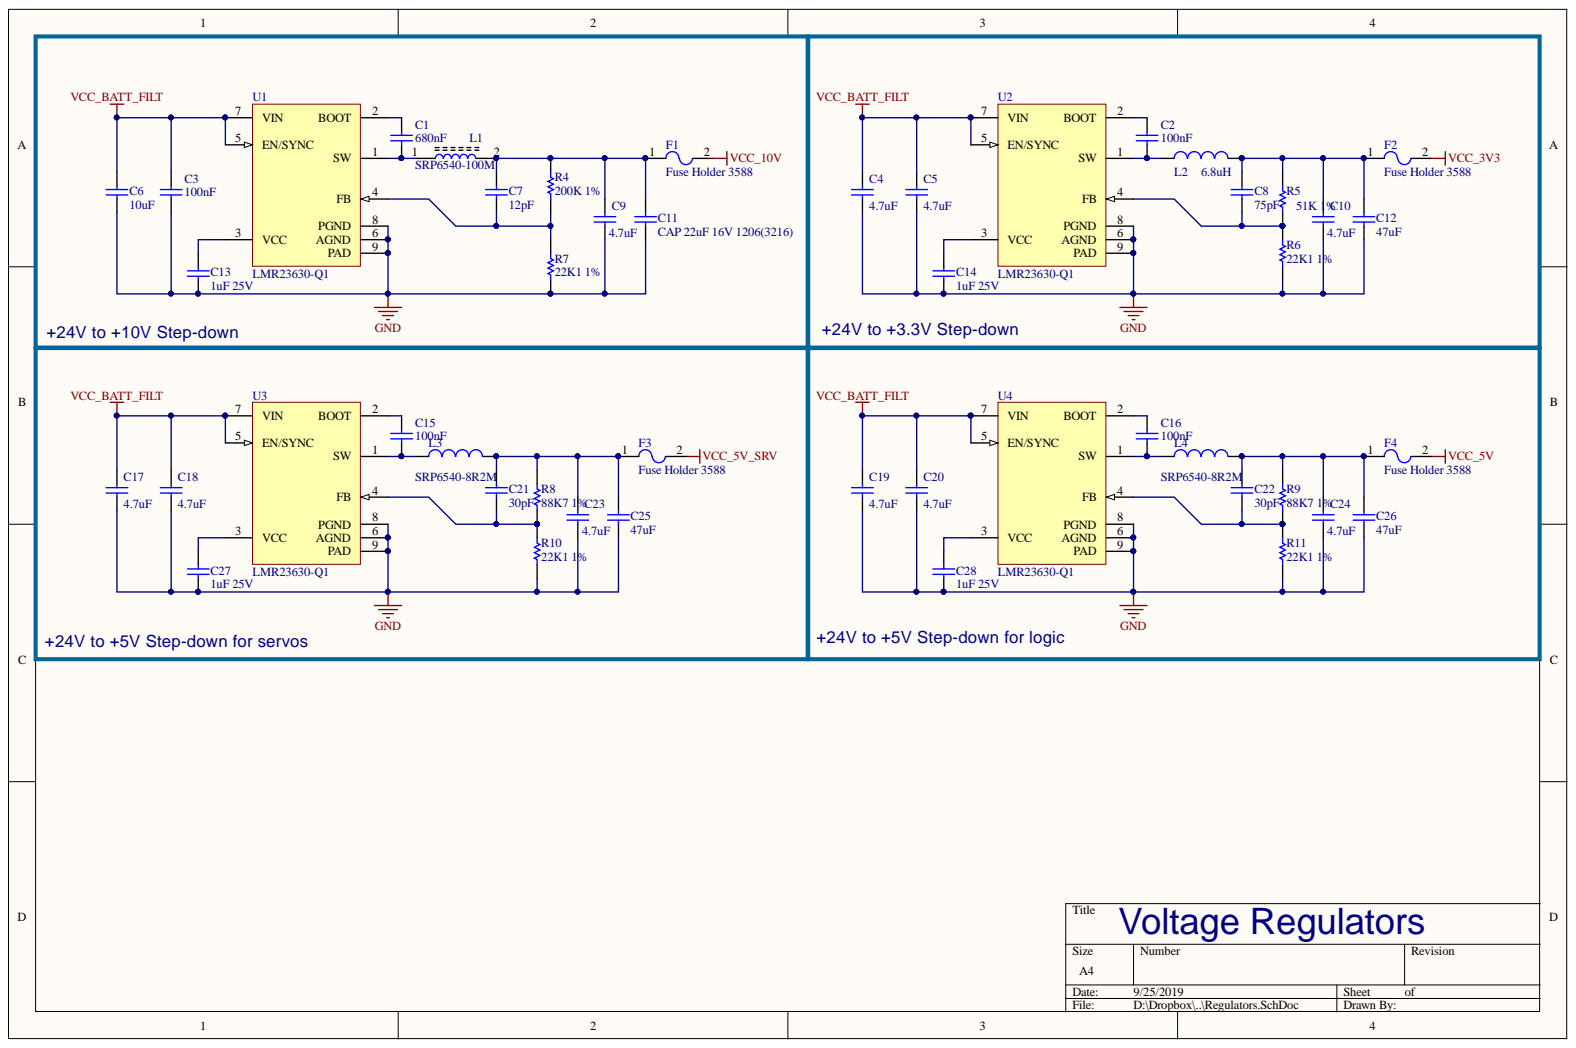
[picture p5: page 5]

Numbe r | R evision

: 9/25/2019 | She et of
File : D:\D ropbox\. .\R egulators. S chDoc | D r a wn By:

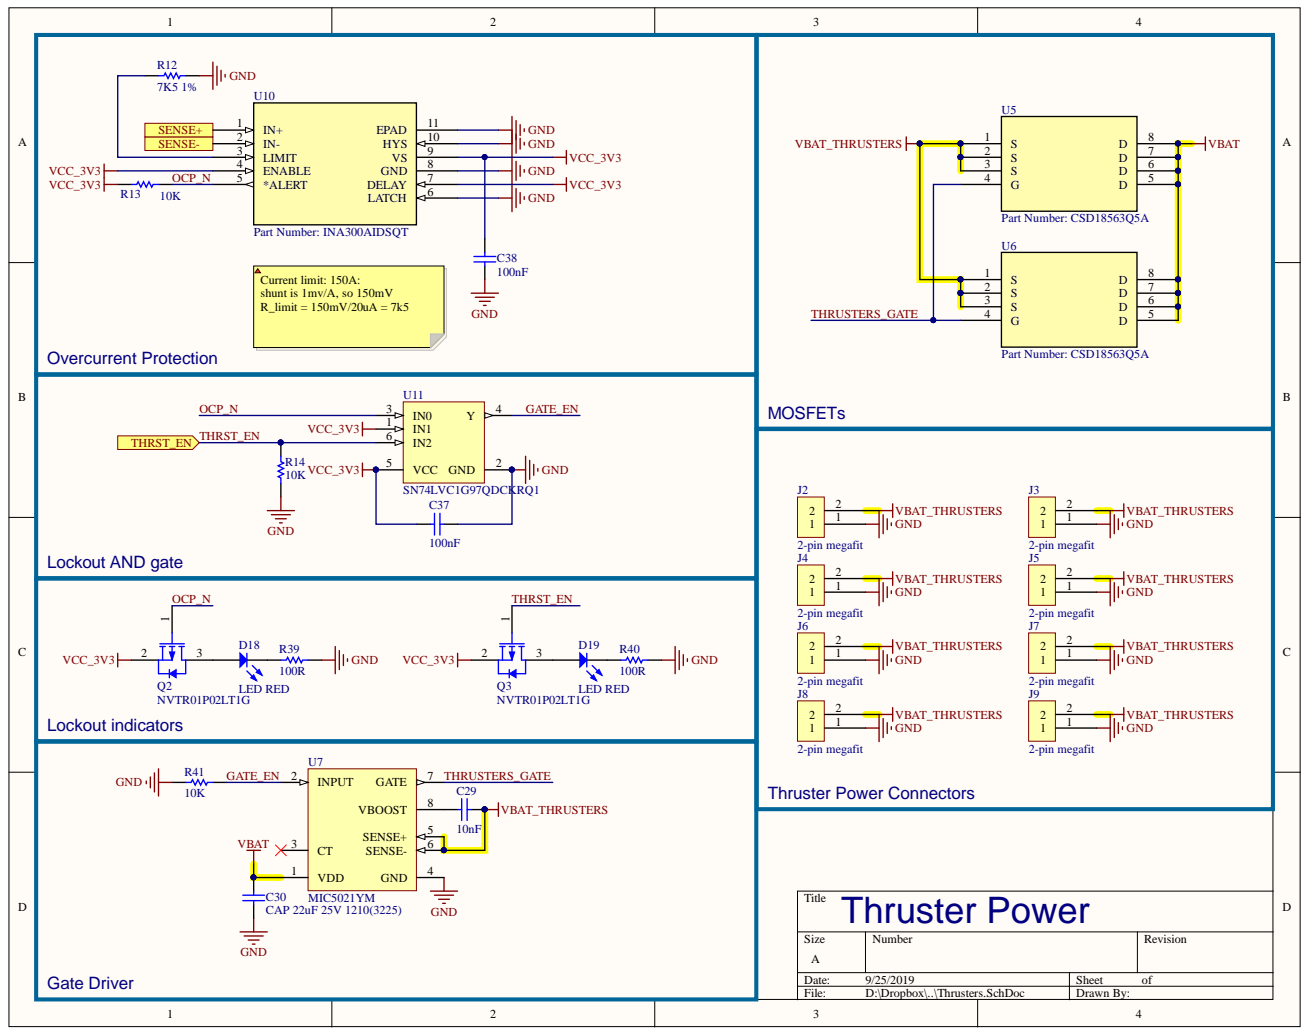
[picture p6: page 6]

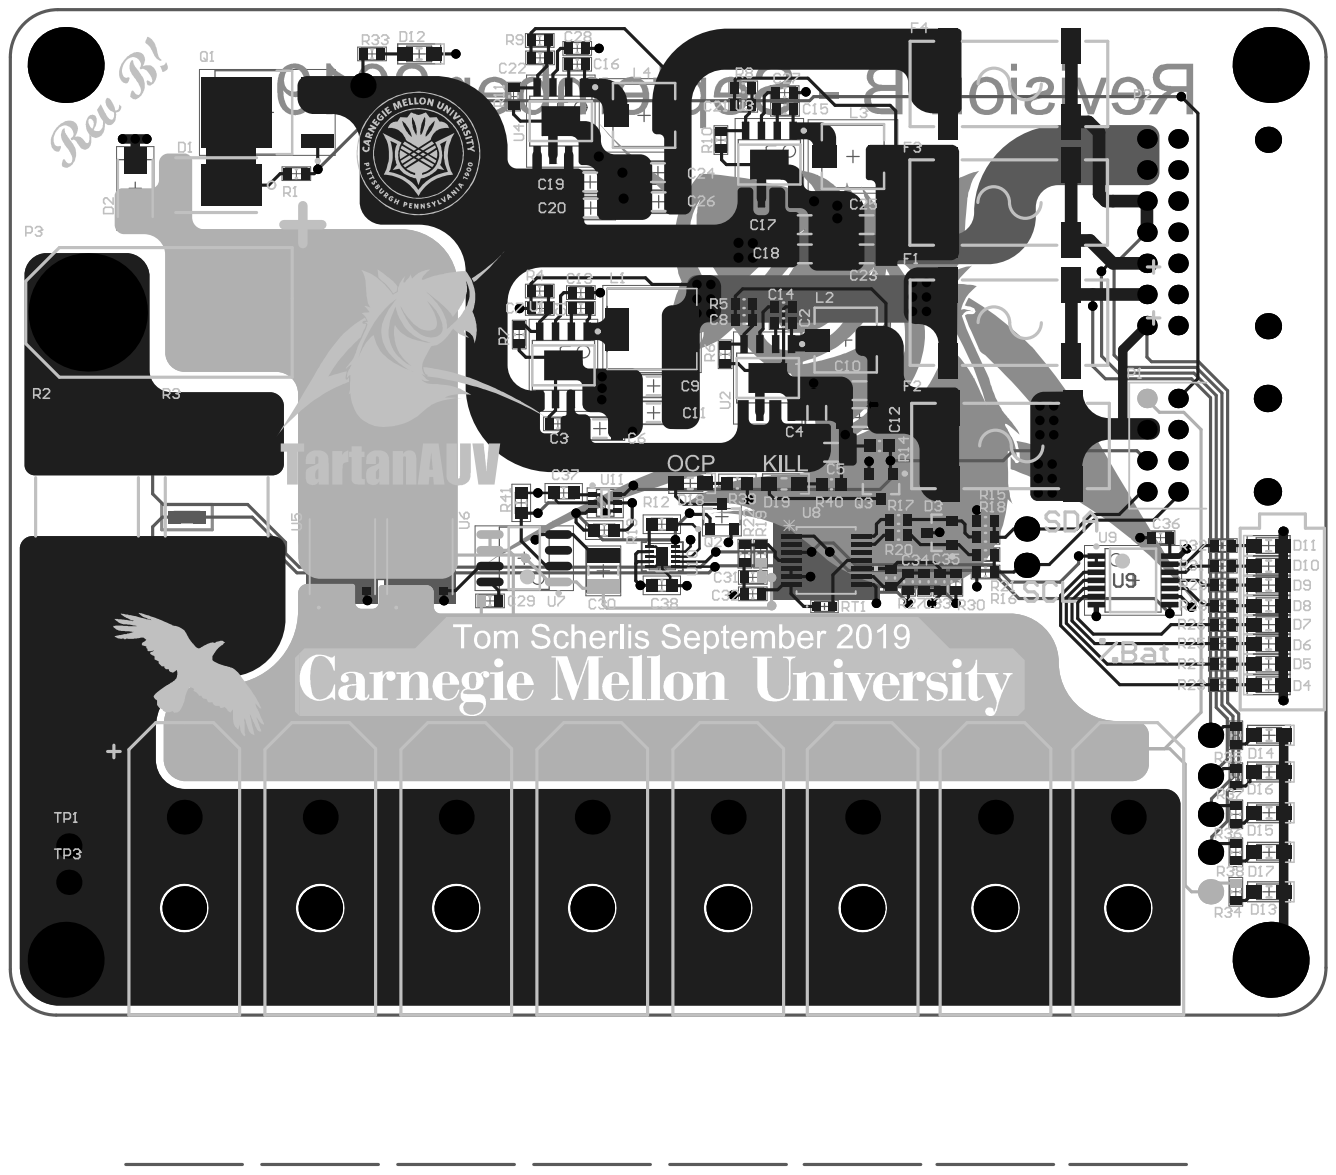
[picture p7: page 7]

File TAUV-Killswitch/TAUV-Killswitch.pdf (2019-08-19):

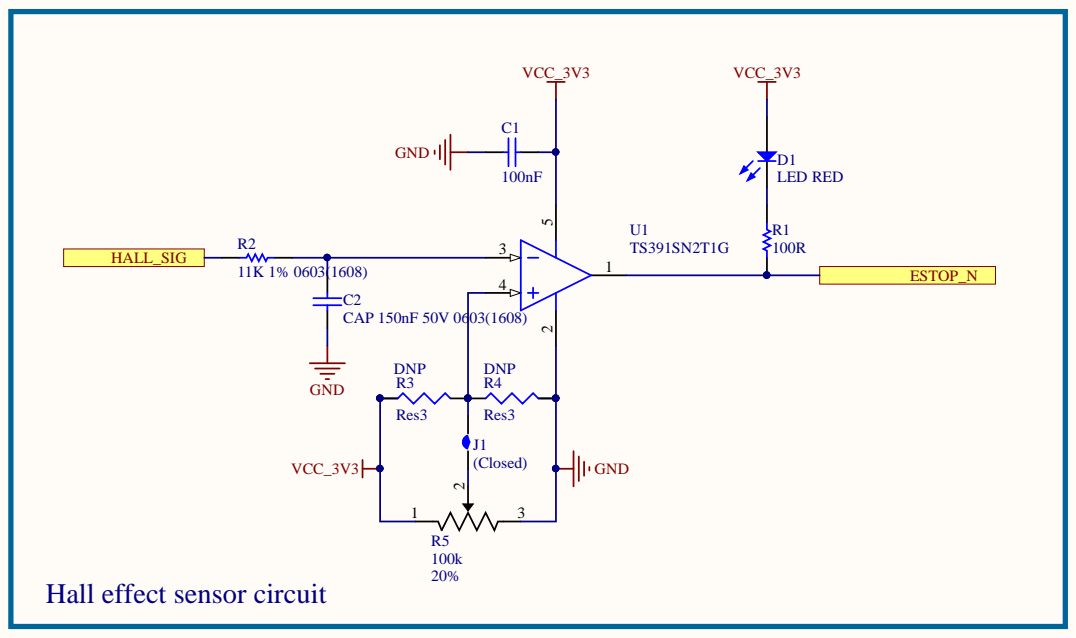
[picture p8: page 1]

Hall effect sensor circuit

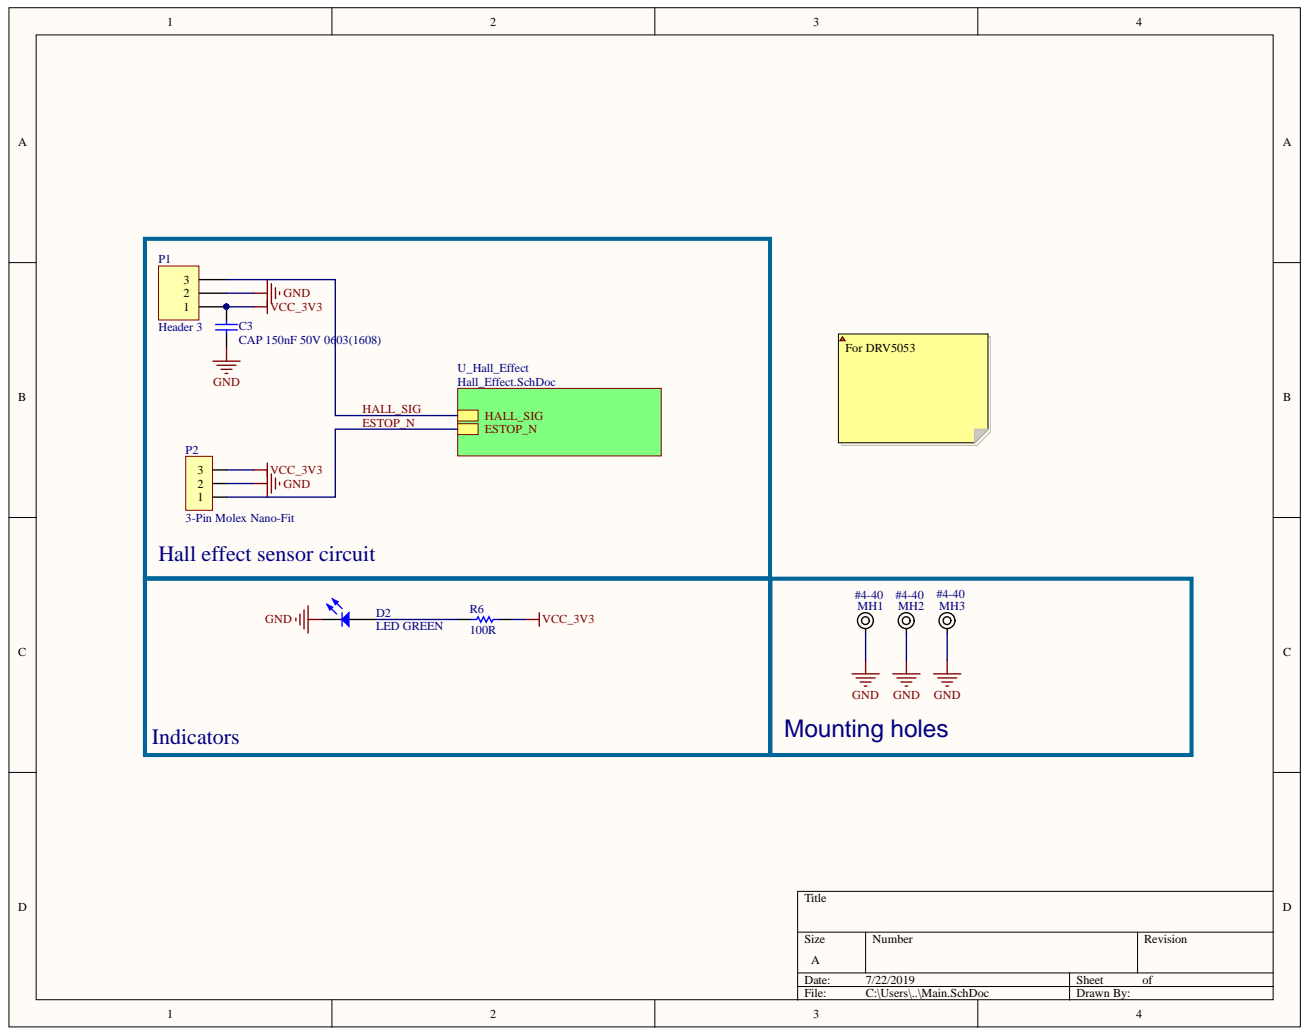
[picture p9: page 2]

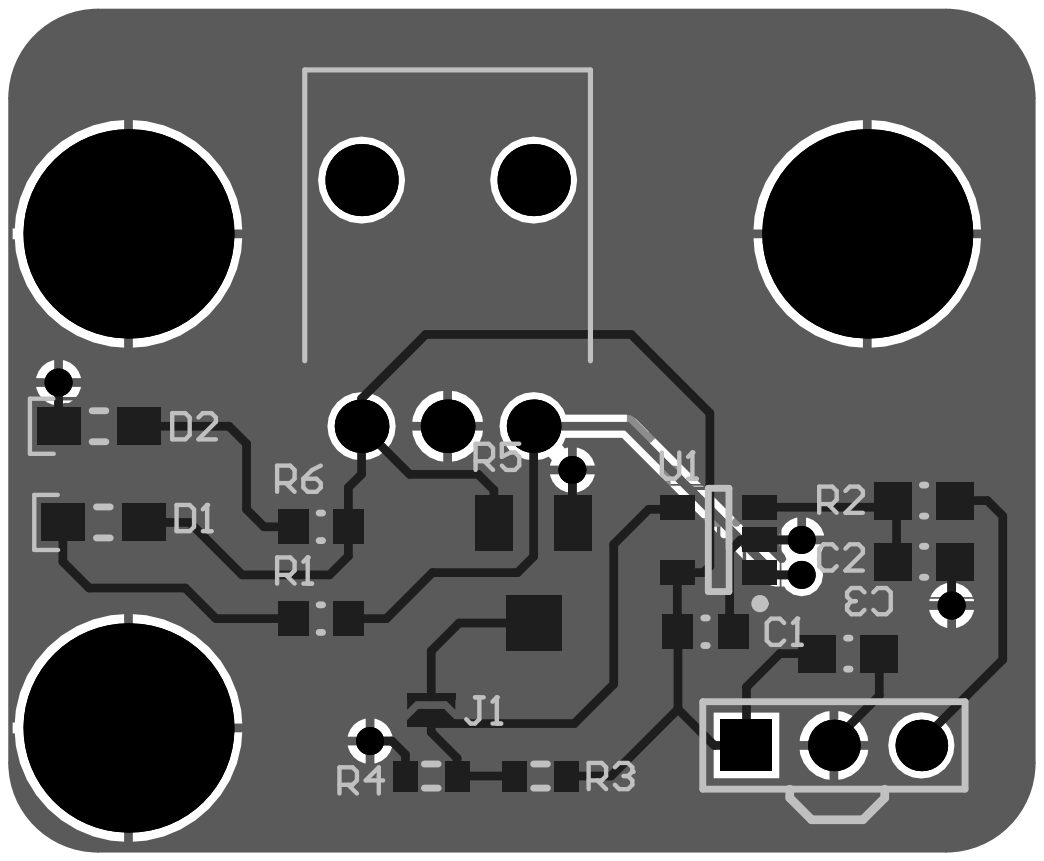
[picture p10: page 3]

# Board Stack R

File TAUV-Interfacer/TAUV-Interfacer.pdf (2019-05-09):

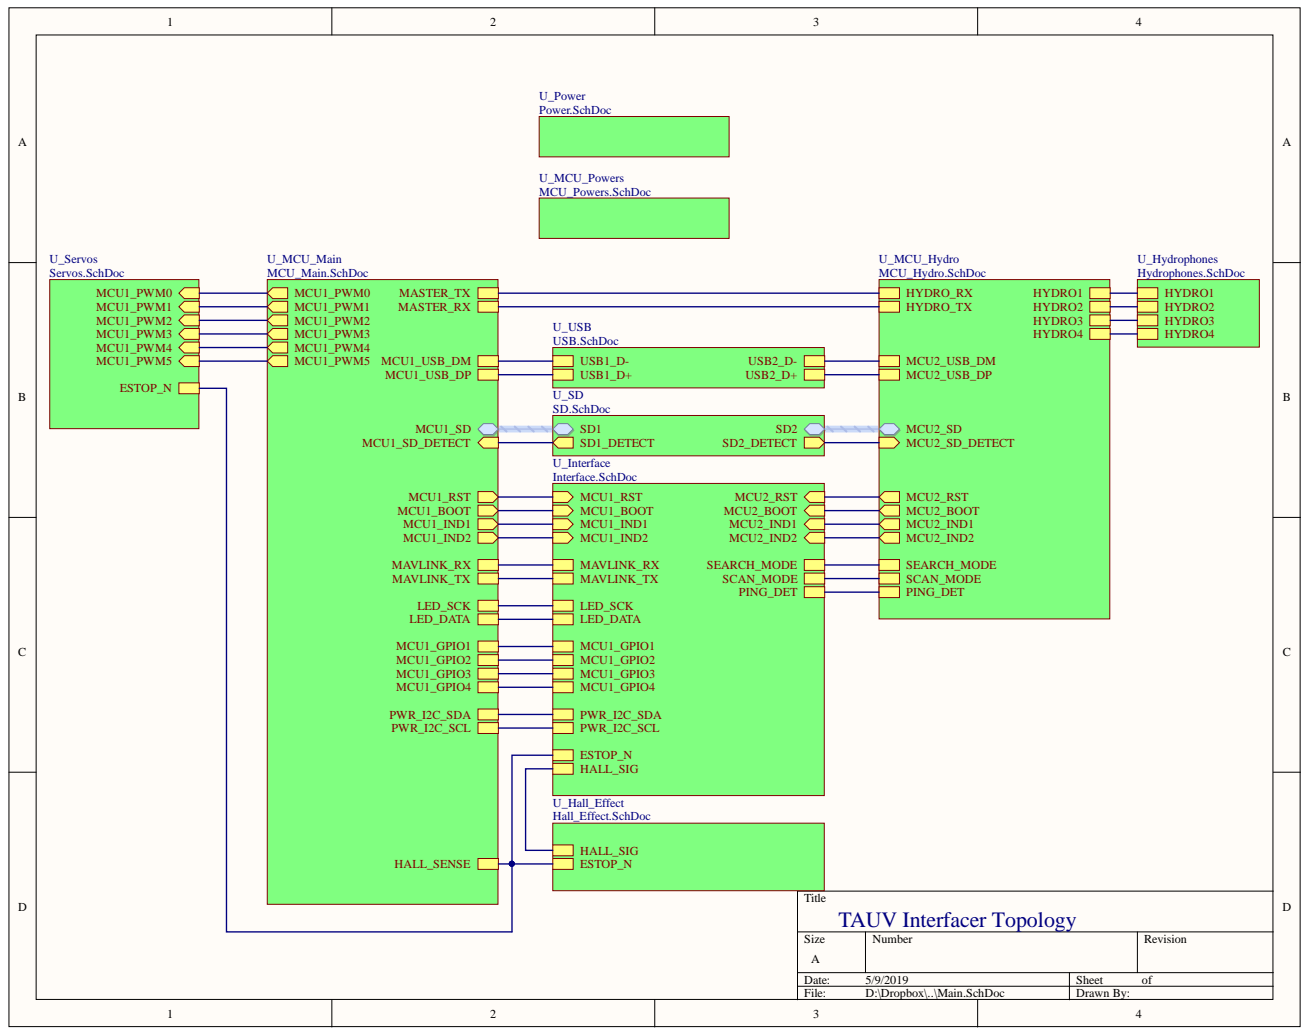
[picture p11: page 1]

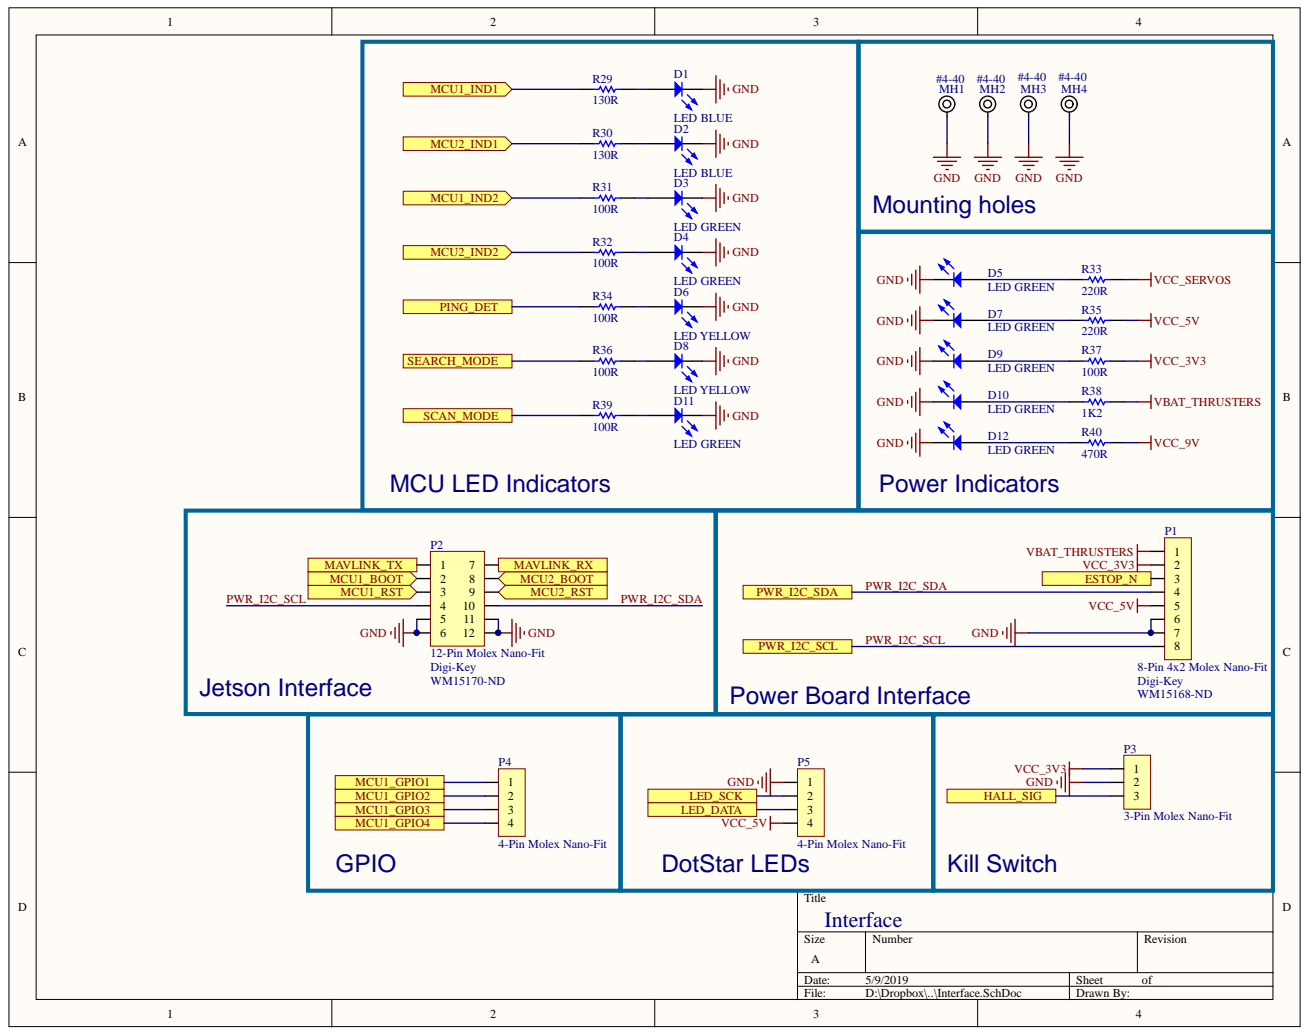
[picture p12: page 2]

Power Indicators

P2 Jetson Interface | P1 8-Pin 4x2 Molex Nano-Fit



Decoupling (1 per VDD pin)


M a v Lin k Interfa

D otStar interfa | | | B

MC U1_P WM0 MC U1_P WM0 MC U1_P WM1 MC U1_P WM1 MC U1_P WM2 MC U1_P WM2 MC U1_P WM3 MC U1_P WM3 MC U1_P WM4 MC U1_P WM4 MC U1_P WM5 MC U1_P WM5 S erv o Interfa c e | S D I O MC U1_S D_C K CLK CMD DAT0 DAT1 DAT2 DAT3 MC U1_S D_D 1 MC U1_S D_D 2 MC U1_S D_DETEC T S D C ard Interfa c e | MC U1_S D MC U1_S D_DETEC T | S U

Numbe r | R evision

: 5/9/2019 | She et of
File : D:\D ropbox\. .\MC U_Main. S chDoc | D r a wn By:


USB FC device interface

Size A4 | Number | Revision

Date: 5/9/2019 | Sheet of
File: D:\Dropbox\..\MCU_Hydro.SchDoc | Drawn By:


max 5v R MS input H Y DRO _IN _4 | low-pas s stage R2 4 R C1 6 G N D | high-pas s and biasing AVCC_ 3 V 3 R2 3 3 K 2 4 1 % C1 5 1 0 n F R2 7 3 K 2 4 1 % G N D | Attenuation and buffering R1 4 K 1 2 | Output R7 9 2 7 0 R


Servo Disconnect gate driver and overcurrent


Hall effect sensor circuit


Note: SDIO Transmission lines must be length
matched with 50 ohm impedence. Maintain equal
numbers of vias per signal. Ground referenced
preferably.



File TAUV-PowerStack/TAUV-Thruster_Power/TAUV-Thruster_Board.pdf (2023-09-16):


Because we don't have a net tie
object, the GND net goes to the
SENSE+ pin, and the PACK-
net goes to the SENSE- pin.

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


LIMIT 3

*ALERT 5


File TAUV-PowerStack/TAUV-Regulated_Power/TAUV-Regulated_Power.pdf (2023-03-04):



Si z e | Num b er | Revi s i on

e : 3/03/ 20 2 3 | Sheet of
Fi l e : Y: \Document s \..\Sht3-Regulator s . S chDo | c D rawn By:


Db o o t1 _ 1 5 0 0 mV | GND


Db o o t1 _2 5 0 0 mV | GND


THRST_EN:pulllow to disable
thrusters. drive to 3v3 to enable.

EXT_EN:pulllow to disable external
power. drive to 3v3 to enable.

REED_P:drive low to enable
electronics. Mustbe done with a
hardware switch.

Ard_A2 | A2 21
Ard_A3 Ard_A4/SDA | A3 22 A4 23

Ard_A5/SCL | A5 24



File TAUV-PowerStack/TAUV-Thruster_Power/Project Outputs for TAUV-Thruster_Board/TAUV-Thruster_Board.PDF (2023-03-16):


Because we don't have a net tie
object, the GND net goes to the
SENSE+ pin, and the PACK-
net goes to the SENSE- pin.

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

Board-to-Board Connector


D 7
D 8






















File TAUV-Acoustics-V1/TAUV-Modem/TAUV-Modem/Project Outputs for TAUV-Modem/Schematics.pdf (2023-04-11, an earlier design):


# Tx Drivers Tx H Bridge


Needs 2 AND gates, 1 NOT gate

## Buffer Power Supply


40kHz/100kHz bandpass filter
Roll your own with op-amps or check out a
ready-made chip like LTC1563. If making from
scratch, look for single-supply designs (TI Single
Supply Op Amp Design Techniques)

Filter Op-Amp Bypass V5+

Filter Op-Amp Bypass

Programmable gain amplifier post-filter
Either use I2C or a few digital inputs from Teensy
to set gain

Output level shifting
Shift 0-5V signal centered at 2.5V to 0-3V3 signal
centered at 1.65V for teensy ADC input

EP should be tied to quiet AGND

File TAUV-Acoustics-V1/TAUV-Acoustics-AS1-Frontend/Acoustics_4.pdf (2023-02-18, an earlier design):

A

B


View from Top side (Scale 1:1)

Notes:
1. Mounting holes are M3 slip fit

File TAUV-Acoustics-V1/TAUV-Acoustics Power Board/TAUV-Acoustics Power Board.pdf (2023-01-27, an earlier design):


Tartan AUV Acoustics Power Board


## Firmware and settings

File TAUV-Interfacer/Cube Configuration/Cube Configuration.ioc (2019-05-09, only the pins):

Mcu.UserName=STM32F746VGTx
PA0/WKUP.Signal=UART4_TX
PA1.Signal=UART4_RX
PA11.Signal=USB_OTG_FS_DM
PA12.Signal=USB_OTG_FS_DP
PA13.Signal=SYS_JTMS-SWDIO
PA14.Signal=SYS_JTCK-SWCLK
PA15.Signal=SYS_JTDI
PA2.Signal=USART2_TX
PA3.Signal=USART2_RX
PA5.Signal=SPI1_SCK
PA7.Signal=SPI1_MOSI
PB0.Signal=S_TIM3_CH3
PB1.Signal=S_TIM3_CH4
PB10.Signal=I2C2_SCL
PB11.Signal=I2C2_SDA
PB3.Signal=SYS_JTDO-SWO
PB6.Signal=I2C1_SCL
PB7.Signal=I2C1_SDA
PC10.Signal=SDMMC1_D2
PC11.Signal=SDMMC1_D3
PC12.Signal=SDMMC1_CK
PC8.Signal=SDMMC1_D0
PC9.Signal=SDMMC1_D1
PD0.Signal=GPIO_Input
PD13.Signal=GPIO_Output
PD14.Signal=GPIO_Output
PD2.Signal=SDMMC1_CMD
PE11.Signal=S_TIM1_CH2
PE13.Signal=S_TIM1_CH3
PE14.Signal=S_TIM1_CH4
PE9.Signal=S_TIM1_CH1
PH0/OSC_IN.Signal=RCC_OSC_IN
PH1/OSC_OUT.Signal=RCC_OSC_OUT

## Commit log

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2019-05-09 add hydrophone supply voltage switcher, different hydrophone connectors
    [Hall_Effect.SchDoc, Hydrophones.SchDoc, Interface.SchDoc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]
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2019-09-05 no longer track debug.log or previews
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2022-08-29 New board Idea and minor changes to pwr board
    [External.SchDoc, Interface.SchDoc, Rylan Power Board.PcbDoc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]
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2023-01-07 Major Updates
    Work done on schematics and board file created
    [TAUV-Powerboard-2023.PcbDoc]
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2023-01-19 Component work
    Finally got CMR library and components into pcb file
    [TAUV-Lib.SchLib]
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2023-02-18 Major updates to board layout and files. 1 of the 2 12V regulators is layed out but not routed
    [Sht2-V12P0.SchDoc, Sht4-Interfaces.SchDoc, Sht5-V12P0_Jetson.SchDoc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]
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2023-02-18 Revised schematic and layout
    Added board-to-board connector (with regulator board) and current shunt. Revised layout.
    [Interfaces.SchDoc, Main.SchDoc, Power.SchDoc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]
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2023-02-27 Almost done (TM)
    Need to place mounting holes and inter board connector for the thruster board
    [Sht4-Interfaces.SchDoc]
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2023-03-02 Thruster board and connector changes
    UMPS and UMPT do not have different current capacity based on the height so the shortest possible connector will be used
    [Interfaces.SchDoc, Power.SchDoc, Sht4-Interfaces.SchDoc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]
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2023-03-03 Inter-board connector added
    Lots of copper needed. using like all of the layers
    [Sht1-BlockDiagram.SchDoc]
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2023-03-04 Finished thruster board layout
    Still need to put mounting holes, and also double check for any design issues
    [Power.SchDoc, TAUV-Thruster_Board.PcbDoc]
2023-03-05 Multi-board design stack started
    Altium Pro is required to manipulate multi-board designs. I will add people to our altium group soon so they have access to these licenses
    [Interfaces.SchDoc, Sht1-BlockDiagram.SchDoc, Sht4-Interfaces.SchDoc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]
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2023-03-05 fixed unrouted net
    [TAUV-Thruster_Board.PcbDoc]
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2023-03-06 Fixed silk and mounting hole clearance issue
2023-03-07 Fixed design rule violations
    [TAUV-Thruster_Board.PcbDoc, TAUV-Thruster_Board.PrjPcb]
2023-03-07 Additional revisions
    Adjusted location of Arduino to allow for headers to easily use arduino pins. Adjusted size of thruster board slightly to ensure clearance. Added battery undervolt LED controlled by arduino. Added notes for how "Smart" rev will operate.
    [Sht2-V12P0_reg.SchDoc, Sht3-Regulators.SchDoc, Sht4-Interfaces.SchDoc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]
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2023-03-08 Changed to a single V12P0
    This is done by recommendation of my father and further research. Due to the high power and complex requirements of the copper layout properly merging the 2 regulators would be extremely complicated
    [Sht1-BlockDiagram.SchDoc, Sht2-V12P0_reg.SchDoc, Sht4-Interfaces.SchDoc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]
2023-03-08 Added voltage sense to all lines and added DNP resistors to allow for configurable sense
    [Sht4-Interfaces.SchDoc, TAUV-Thruster_Board.PcbDoc]
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2023-03-14 Silkscreen tweaks
    Added labels for the PACK- and VBAT pins, and for the OCP and THRST_EN LEDs. Changed solder mask color to black. Fixed design rule violations.
    [TAUV-Thruster_Board.PcbDoc]
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2023-03-18 Changed U2 configuration to an AND gate
    Connected pin 1 on U2 to GND instead of VCC, configuring U2 to be an AND gate.
    [Interfaces.SchDoc, TAUV-Thruster_Board.PcbDoc]
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2023-03-25 Finished schematics
    Finished the schematics for the phod board, added nanofit connectors
    [Interface.SchDoc, Main.SchDoc, Op-Amp Stages.SchDoc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]
2023-03-26 Updated layout
    Made a lot of progress on the phod board layout. To-do: Output connectors, 3V3/2 reference, ground pours
    [Amplifiers.SchDoc, Interface.SchDoc, Main.SchDoc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]
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2023-04-06 (almost) finished layout
    Almost done with the phod board layout, just need some final touches
    [Interface.SchDoc, Main.SchDoc, TAUV-PHOD-Board.PcbDoc]
2023-04-07 Finished layout
    Finished the layout for the phod board. Exported a .pdf of the files for easy viewing. Pending final design review.
    [Interface.SchDoc, Main.SchDoc, TAUV-PHOD-Board.PcbDoc]
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2023-04-09 Revised PHOD board
    Changed PGAs to 4x LTC6910 instead of 2x LTC6912. Also added a diode clamp to the input of the 1st stage. Remade board layout.
    [Amplifiers.SchDoc, Interface.SchDoc, Main.SchDoc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]
2023-04-09 Generated gerber files
    Applied final touches to the board and generated gerber X2 files for export.
    [Main.SchDoc, TAUV-PHOD-Board.PcbDoc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]
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2023-04-11 Added mounting holes
    Added M3 screw mounting holes. Updated .pdf schematic/PCB outputs.
    [TAUV-PHOD-Board.PcbDoc, TAUV-PHOD-Board.PrjPcb]
2023-04-11 Updated mounting holes
    Redid mounting holes to fit the acoustics power board
    [TAUV-PHOD-Board.PcbDoc]
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2023-05-14 Redesigned after testing
    Redesigned the thruster board after finding errors during testing. Flipped the Mosfets so the drain is connected to VBAT, to stop them from conducting thru the body diode. Changed the relevant passives. Added a 10 Ohm resistor Rs to ground the gate driver's sense pin. Added silkscreen labels for THRUST_EN and OCP_N.
    [Power.SchDoc, TAUV-Thruster_Board.PcbDoc]
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2023-05-26 Added 9th connector
    Added a 9th thruster connector to power the suction arm thruster. Needed to make the board slightly wider to fit it.
    [Interfaces.SchDoc, TAUV-Thruster_Board.PcbDoc]
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2023-06-10 Added 2nd board-to-board connector
    Added a 4-pin Samtec UMPS connector to give VBAT_THRUSTERS and SENSE+ to the regulator board. Two of the pins are free and can be used for something else.
    [Interfaces.SchDoc, TAUV-Thruster_Board.PcbDoc]
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2023-06-11 Fixed Min hole size to .3mm to lower PCB manufacturing cost
    [Bill of Materials-TAUV-Regulated_Power.csv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]
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2023-06-20 Made thruster board less wide
    I shaved off a few mms in width from the thruster board so that it fits on the regulator board more nicely. I also made some silkscreen tweaks.
    [TAUV-Thruster_Board.PcbDoc]
2023-06-23 Swapped to old regulator footprint for V5P0 and V3P3
    [Sht2-V12P0_reg.SchDoc, Sht3-Regulators.SchDoc]
2023-06-23 fixed file structure
    [Sht1-BlockDiagram.SchDoc, Sht2-Regulators.SchDoc, Sht2-V12P0_reg.SchDoc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]
2023-06-23 Post Design Review changes
    Got suggestions from coworkers and applied to the board/schematics
    [Sht2-Regulators.SchDoc, Sht3-V12P0_reg.SchDoc, Sht4-Interfaces.SchDoc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]
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2023-07-03 Updated BOM, fixed design rule violations
    Updated the BOM to include component links, and fixed some minor design rule violations
    [Bill of Materials-TAUV-Thruster_Board.csv, TAUV-Thruster_Board BOM.xlsx]
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2023-09-21 Project was moved to the native VCS repository (Versioned Storage) in your Altium Server. Your local project (local repository) now needs to be switched to point to this new remote repository. Please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
    [TAUV_Acoustics_V2.PrjPcb]
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2023-09-21 Revert "File structure updates"
    This reverts commit c5972e12d05f50aad86ef15db31aaeefbdbed323.
    [BMS.SchDoc, Bill of Materials-TAUV-Powerboard.xls, Bill of Materials-TAUV-Regulated_Power- 4_6.xlsx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]
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2023-10-10 Added a bunch of stuff
    pspice simulations of LT1210 + transformer transmitter.
    Pspice of an OPA547-based impedance measurement circuit.
    MATLAB impedance curve calculator.
    Sweep data for a new transducer (two sweeps, Rshunt=177.8k).
    Basic COMSOL frequency response / impedance analysis
    [FRONTEND-DESIGN-CANDIDATES.DSN, TRANSDUCER-CHARACTERIZATION.DSN, td_char_177.8.csv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]
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
